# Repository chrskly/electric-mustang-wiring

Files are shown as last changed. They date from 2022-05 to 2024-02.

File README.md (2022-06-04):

# Electric Mustang Wiring

This repo contains the circuits, software, and wiring diagrams for my project to
convert a 1965 Ford Mustang to a EV.

## bms - Battery Management System

Schematic, PCB, and software for the battery management system.

## 12v-front-pcb

Schematic and PCB for wiring that sits in the front of the car (engine bay).

* Ignition switch
* Drive inhibition (preventing driving off when charging)
* Coolant pump
* Inverter
* Contactors
* Shunt

## 12v-lighting

Schematic and PCB for wiring for all of the lighting.

* Headlights/highbeams
* Indicators
* Brake lights
* Interior lights

## 12v-rear-pcb

Schematic and PCB for wiring that sits in the rear of the car (boot).

* On-board AC charger
* DC charger
* Charger VCU

## dashboard-vcu

Schematic and PCB for VCU to control the car dashboard.

## dashboard-vcu-src

Source code of dashboard vcu firmware.

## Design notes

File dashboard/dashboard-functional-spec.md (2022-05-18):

# Functional spec for dashboard

I want the interior of the car to remain original, or, at least, feel original.
No screens. The existing gauges and dash lights are more than enough to use the
car for normal driving. The dashboard will provide an additional web interface
for when I need to inspect the details of the cars operation.

Dashboard will need to stay on all of the time, but can possibly switch to a
lower power mode when car is not driving/charging.

## Physical dash functionality

1. Read SoC from ISA shunt and show on fuel gauge.

2. Show max of all temps on temp gauge (what temps will be available?)

3. Show car mode on left dash indicator.
  - Orange : ignition on, but inverter not in run mode
  - Green  : ignition on, inverter in run mode
  - Blue   : charging

4. Show car status on right dash indicator.
  - Green  : car healthy
  - Orange : warning message from one of the car systems
  - Red    : critical error from one of the car systems

Note : I could possibly show all of this with one dash light. If so, what would
I use the other one for?

5. Stepper motor to drive speedo/odometer.

6. Data logger.

7. GPS?

## Web dash functionality

1. Provide WiFi hotspot. esp8266 or similar.

2. Show pack voltage.

3. Show pack SoC.

4. Show current power in/out.

5. Charging : status

6. Charging : eta to 80%, 100%

7. Driving : estimated range, time to empty.

8. Logs

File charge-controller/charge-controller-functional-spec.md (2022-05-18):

# Functional spec for charge controller

Charge controller will manage LIM unit for DC charging and Tesla v2 unit for
AC charging.

## Functionality

1. Measure temp of charge port.

2. Limit charging rate based on battery temp.

## Connections

1. CAN port connected to main CAN bus.

2. CAN port connected to Tesla gen 2 OBC.

3. CAN port connected to LIM.

4. 2x thermistor inputs.

5. Stop charge input.

## CAN messages consumed by charge controller

1. BMS temperature readings.

## CAN messages produced by charge controller

1. Control messages for LIM

2. Control messages for Tesla charger

## External resources

### Damien's LIM control implementation for Zombieverter

https://github.com/damienmaguire/Stm32-vcu/blob/master/src/i3LIM.cpp

### OpenInverter forum LIM docs

https://openinverter.org/wiki/BMW_I3_Fast_Charging_LIM_Module

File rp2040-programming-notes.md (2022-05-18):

## Pinout

http://land-boards.com/blwiki/images/thumb/5/56/Raspberry-Pi-Pico-Pinout.jpg/730px-Raspberry-Pi-Pico-Pinout.jpg

## Repeating timers

https://emalliab.wordpress.com/2021/04/18/raspberry-pi-pico-arduino-core-and-timers/

https://raspberrypi.github.io/pico-sdk-doxygen/group__repeating__timer.html#ga02133dbe7083fcf3c7392a2cfb8243ba

## Changing PWM frequency

https://www.pschatzmann.ch/home/2021/05/19/back-to-basics-audio-output-on-the-raspberry-pico/

## mcp2515

https://github.com/autowp/arduino-mcp2515

https://github.com/adamczykpiotr/pico-mcp2515

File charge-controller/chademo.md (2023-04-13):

# Chademo

## Chademo pinout

 1. Ground
 2. CP : evse => car, IN1, contactor +ve signal, goes high when active, sensed by 'f'
 3. nc
 4. CP3 : car => evse, OUT1, charge enable, sensed by 'k'
 5. HV-
 6. HV+
 7. CS : connection check, goes low when plug inserted, sensed by 'h'
 8. CAN H
 9. CAN L
10. CP2 : evse => car, IN2, contactor -ve signal, goes low when active, sensed by 'g'

OUT2, contactor override, pull low to allow CP2 signal through

## Charging sequence

- station pulls CS high?low? to indicate plug insertion
- station pulls CP high (IN1), d1 closes, +ve contactor closes
- Start CAN
- Station/car send params, compatability check
- car pulls CP3 low to indicate start permission
- connector lock
- station runs insulation test
- station pulls CP2 low (IN2), d2 closes
- << charging >>
- car sends current request constantly
- battery fills up, car sends zero current request
- car deactivates CP3, stop permission
- station deactivates CP and CP2
- weld detection?
- unlock

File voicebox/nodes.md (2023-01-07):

https://gregchadwick.co.uk/blog/playing-with-the-pico-pt3/

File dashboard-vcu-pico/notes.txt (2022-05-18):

https://raspberrypi.github.io/pico-sdk-doxygen/modules.html
https://raspberrypi.github.io/pico-sdk-doxygen/rp2__common_2hardware__spi_2include_2hardware_2spi_8h.html
http://docs.longan-labs.cc/1030018/
https://www.hackster.io/fhdm-dev/use-arduino-libraries-with-the-rasperry-pi-pico-c-c-sdk-eff55c
https://fhdm-dev.github.io/pico-arduino-compat/libraries.html
https://github.com/fhdm-dev/pico-arduino-compat/tree/master/libs/adafruit-ssd1306
https://github.com/107-systems/107-Arduino-MCP2515

https://copperhilltech.com/pican-2-can-bus-interface-for-raspberry-pi/
https://copperhilltech.com/blog/obdii-data-logging-with-raspberry-pi-and-pican2-can-bus-interface/
https://copperhilltech.com/blog/troubleshooting-your-pican2-can-interface-board-for-raspberry-pi/

### Pico PIO
https://www.digikey.com/en/maker/projects/raspberry-pi-pico-and-rp2040-cc-part-3-how-to-use-pio/123ff7700bc547c79a504858c1bd8110

### Pico SDK
https://raspberrypi.github.io/pico-sdk-doxygen/group__hardware__gpio.html#ga594e390dc5e7407a35bcce6cae73ae2c

### Catphish bms
https://github.com/catphish/ev-charge-controller/blob/master/firmware-pico/bms.c

### Getting started with Pico
https://datasheets.raspberrypi.com/pico/getting-started-with-pico.pdf

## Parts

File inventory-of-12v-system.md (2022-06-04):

# Inventory of 12v system

## Engine bay (front-12v)
- [x] Ignition
- [x] Inverter
- [x] ISA shunt (always on)
- [x] Contactors
- [x] Coolant pump
- [x] Drive inhibit

## Cabin
- [ ] Brake
- [ ] Radio
- [ ] Cabin water heater
- [ ] Cabin fan
- [ ] Dashboard (always on)
- [ ] Horn
- [ ] Wipers
- [ ] Cruise

## Lights
- [x] Headlights/highbeams (10A)
- [x] Indicators
- [x] Flashers
- [ ] Brake lights
- [ ] Reverse light
- [x] Cabin light (+glovebox)
- [ ] Engine bay light

## Rear
- [ ] Trunk light
- [ ] Tesla
- [ ] LIM
- [ ] BMS (always on)

## Others
- [ ] Vacuum pump
- [ ] Heated seats

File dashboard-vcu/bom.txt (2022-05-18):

Component, Value, Part #, Footprint
U1, rPi Pico
D2, n/a, SS54B, DIOM5336X244N
PS1, n/a, TPS62160DGKT, TPS62160DGKT
C1, 10uF, CL10A106KP8NNNC, 
C2, 22uF, 
L1, 2.2uH, NR6028T2R2N, 
R1, 1k
R2, R3, 2k2,
R4 + R5 + R6 + R7 + R8 + R9, 220, 
R10, 100k, 
R11, 220k,
R12, 47k, 

J1, Molex 39300140

https://datasheet.lcsc.com/lcsc/2004061032_MOLEX-39300140_C492360.pdf
https://jlcpcb.com/parts/componentSearch?isSearch=true&searchTxt=XAL6030-222MEB
https://www.electronicshub.org/arduino-mcp2515-can-bus-tutorial/
https://www.sparkfun.com/datasheets/DevTools/Arduino/MCP2515.pdf
https://imgur.com/a/pi17C7X

https://www.digikey.be/en/maker/projects/raspberry-pi-pico-rp2040-spi-example-with-micropython-and-cc/9706ea0cf3784ee98e35ff49188ee045

https://raspberrypi.github.io/pico-sdk-doxygen/modules.html

Ampseal35, 1.3mm tin 8A, 1.3mm gold 17A

8 circuit molex, high current connections
https://ie.rs-online.com/web/p/pcb-headers/1615968
https://ie.rs-online.com/web/p/pcb-headers/1615961
https://www.molex.com/molex/products/part-detail/pcb_headers/1720650208
https://www.molex.com/molex/products/part-detail/crimp_housings/1700010108
https://www.molex.com/molex/products/part-detail/crimp_terminals/1720630311
https://componentsearchengine.com/part-view/172065-0208/Molex

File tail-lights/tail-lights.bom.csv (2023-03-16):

Comment | Designator | Footprint | LCSC
HL-AM-2835H421W-S1-08-HR3 | LED1,LED2,LED3,LED4,LED5,LED6,LED7,LED8,LED9,LED10,LED11,LED12,LED13,LED14,LED15,LED16,LED17,LED18,LED19,LED20,LED21,LED22,LED23,LED24,LED25,LED26,LED27,LED28,LED29,LED30,LED31,LED32,LED33,LED34,LED35,LED36,LED37,LED38,LED39,LED40,LED41,LED42,LED43,LED44,LED45,LED46,LED47,LED48,LED49,LED50,LED51,LED52,LED53,LED54,LED55,LED56,LED57,LED58,LED59,LED60,LED61,LED62,LED63,LED64,LED65,LED66,LED67,LED68,LED69,LED70,LED71,LED72 | SMD2835 | C210318
NCV8402ASTT1G | IC2,IC3,IC4 | SOT223 | C77755
ATMEGA328P-AU | IC1 | TQFP-32 | C14877
4k7Ω | R1,R2,R3 | 0805_R | C17673
1k5Ω | R4,R5,R6 | 0805_R | C4310
1uF | C1,C2,C3 | 0805_C | C28323
X322516MLB4SI | Y1 | SMD3225-4P | C13738
10kΩ | R7,R8,R9 | 0805_R | C84376
0.1uF | C4,C5 | 0805_C | C49678
TPS62160DGKR | IC5 | MSOP-8 | C60726
10uF | C6 | 0805_C | C15850
100kΩ | R10 | 0805_R | C149504
2.2uH | L1 | SMD | C135262
220kΩ | R11 | 0805_R | C17539
47kΩ | R12 | 0805_R | C17713
22uF | C7 | 0805_C | C2835558

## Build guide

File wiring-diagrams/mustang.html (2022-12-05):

# mustang

## Diagram

## Bill of Materials

Id | Description | Qty | Unit | Designators
1 | Cable, 1 x 1 mm² | 0 | m | IGNITION_START, W14
2 | Cable, 1 x 6 mm² | 0 | m | W5, W6
3 | Cable, 2 x 1 mm² | 0 | m | IGNITION, W12, W13, W15, W22, W26, W28, W8
4 | Cable, 2 x 10 mm² | 0 | m | W27
5 | Cable, 2 x 35 mm² | 0 | m | W10, W23, W24, W25
6 | Cable, 2 x 6 mm² | 0 | m | W3
7 | Cable, 2 x 70 mm² | 0 | m | W29, W30
8 | Cable, 3 x 1 mm² | 0 | m | W7
9 | Cable, 3 x 2.5 mm² | 0 | m | W16, W17, W18, W19, W20, W21
10 | Cable, 4 x 0.25 mm² | 0 | m | W4
11 | Cable, 4 x 1 mm² | 0 | m | W11, W9
12 | Cable, 8 x 0.25 mm² shielded | 0 | m | W1, W2
13 | Connector, 10 pins | 1 | | TESLA_CHARGER_A
14 | Connector, 12 pins | 1 | | TESLA_CHARGER_B
15 | Connector, 2 pins | 7 | | CHADEMO_CHARGE_PORT, CHARGER_FUSE_1, CHARGER_FUSE_2, CHARGER_FUSE_3, CHARGER_MCB_1, CHARGER_MCB_2, CHARGER_MCB_3
16 | Connector, 2pin, 2 pins | 1 | | 12VBATT
17 | Connector, 3 pins | 1 | | LIM_VOLTAGE_SENSE_2
18 | Connector, 4 pins | 1 | | LIM_VOLTAGE_SENSE_1
19 | Connector, 6 pins | 4 | | FRONT_BATTERY_BOX, REAR_BATTERY_BOX, TESLA_CHARGER_AC, TESLA_CHARGER_DC
20 | Connector, 8 pins | 1 | | CCS_HVJB
21 | Connector, 8pin, 31 pins | 1 | | HVJB
22 | Connector, 8pin, male, 8 pins | 2 | | MG1RES, MG2RES
23 | Connector, 9 pins | 1 | | CCS_CHARGE_PORT
24 | Connector, Ampseal-35, male, 35 pins | 1 | | AMPSEAL_35_1
25 | Connector, Hirschmann 805-587-545, 16 pins | 1 | | LIM_1B
26 | Connector, Molex MegaFit, 2 pins | 8 | | 12V_REAR_J2, 12V_REAR_J3, 12V_REAR_J4, 12V_REAR_J5, 12V_REAR_J6, 12V_REAR_J7, 12V_REAR_J8, 12V_REAR_J9
27 | Connector, Molex MegaFit, 4 pins | 1 | | 12V_REAR_J10
28 | Connector, Molex MegaFit, male, 2 pins | 3 | | 12V_FRONT_J1, 12V_FRONT_J5, 12V_FRONT_J7
29 | Connector, Molex MegaFit, male, 4 pins | 4 | | 12V_FRONT_J2, 12V_FRONT_J3, 12V_FRONT_J4, 12V_FRONT_J6
30 | Connector, SUMITOMO 90980-12362, 8 pins | 1 | | SHIFTER
31 | Connector, Switch, 3 pins | 1 | | IGNITION_SW
32 | Connector, TE 1-967616-1, 6 pins | 1 | | LIM_2B
33 | Connector, TE 1534152-1, 12 pins | 1 | | LIM_4B

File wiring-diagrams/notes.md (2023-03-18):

Colors
WH white
BN brown
GN green
BK black
RD red
YE yellow
BU blue
OG orange
VT violet
GD gold
GY grey

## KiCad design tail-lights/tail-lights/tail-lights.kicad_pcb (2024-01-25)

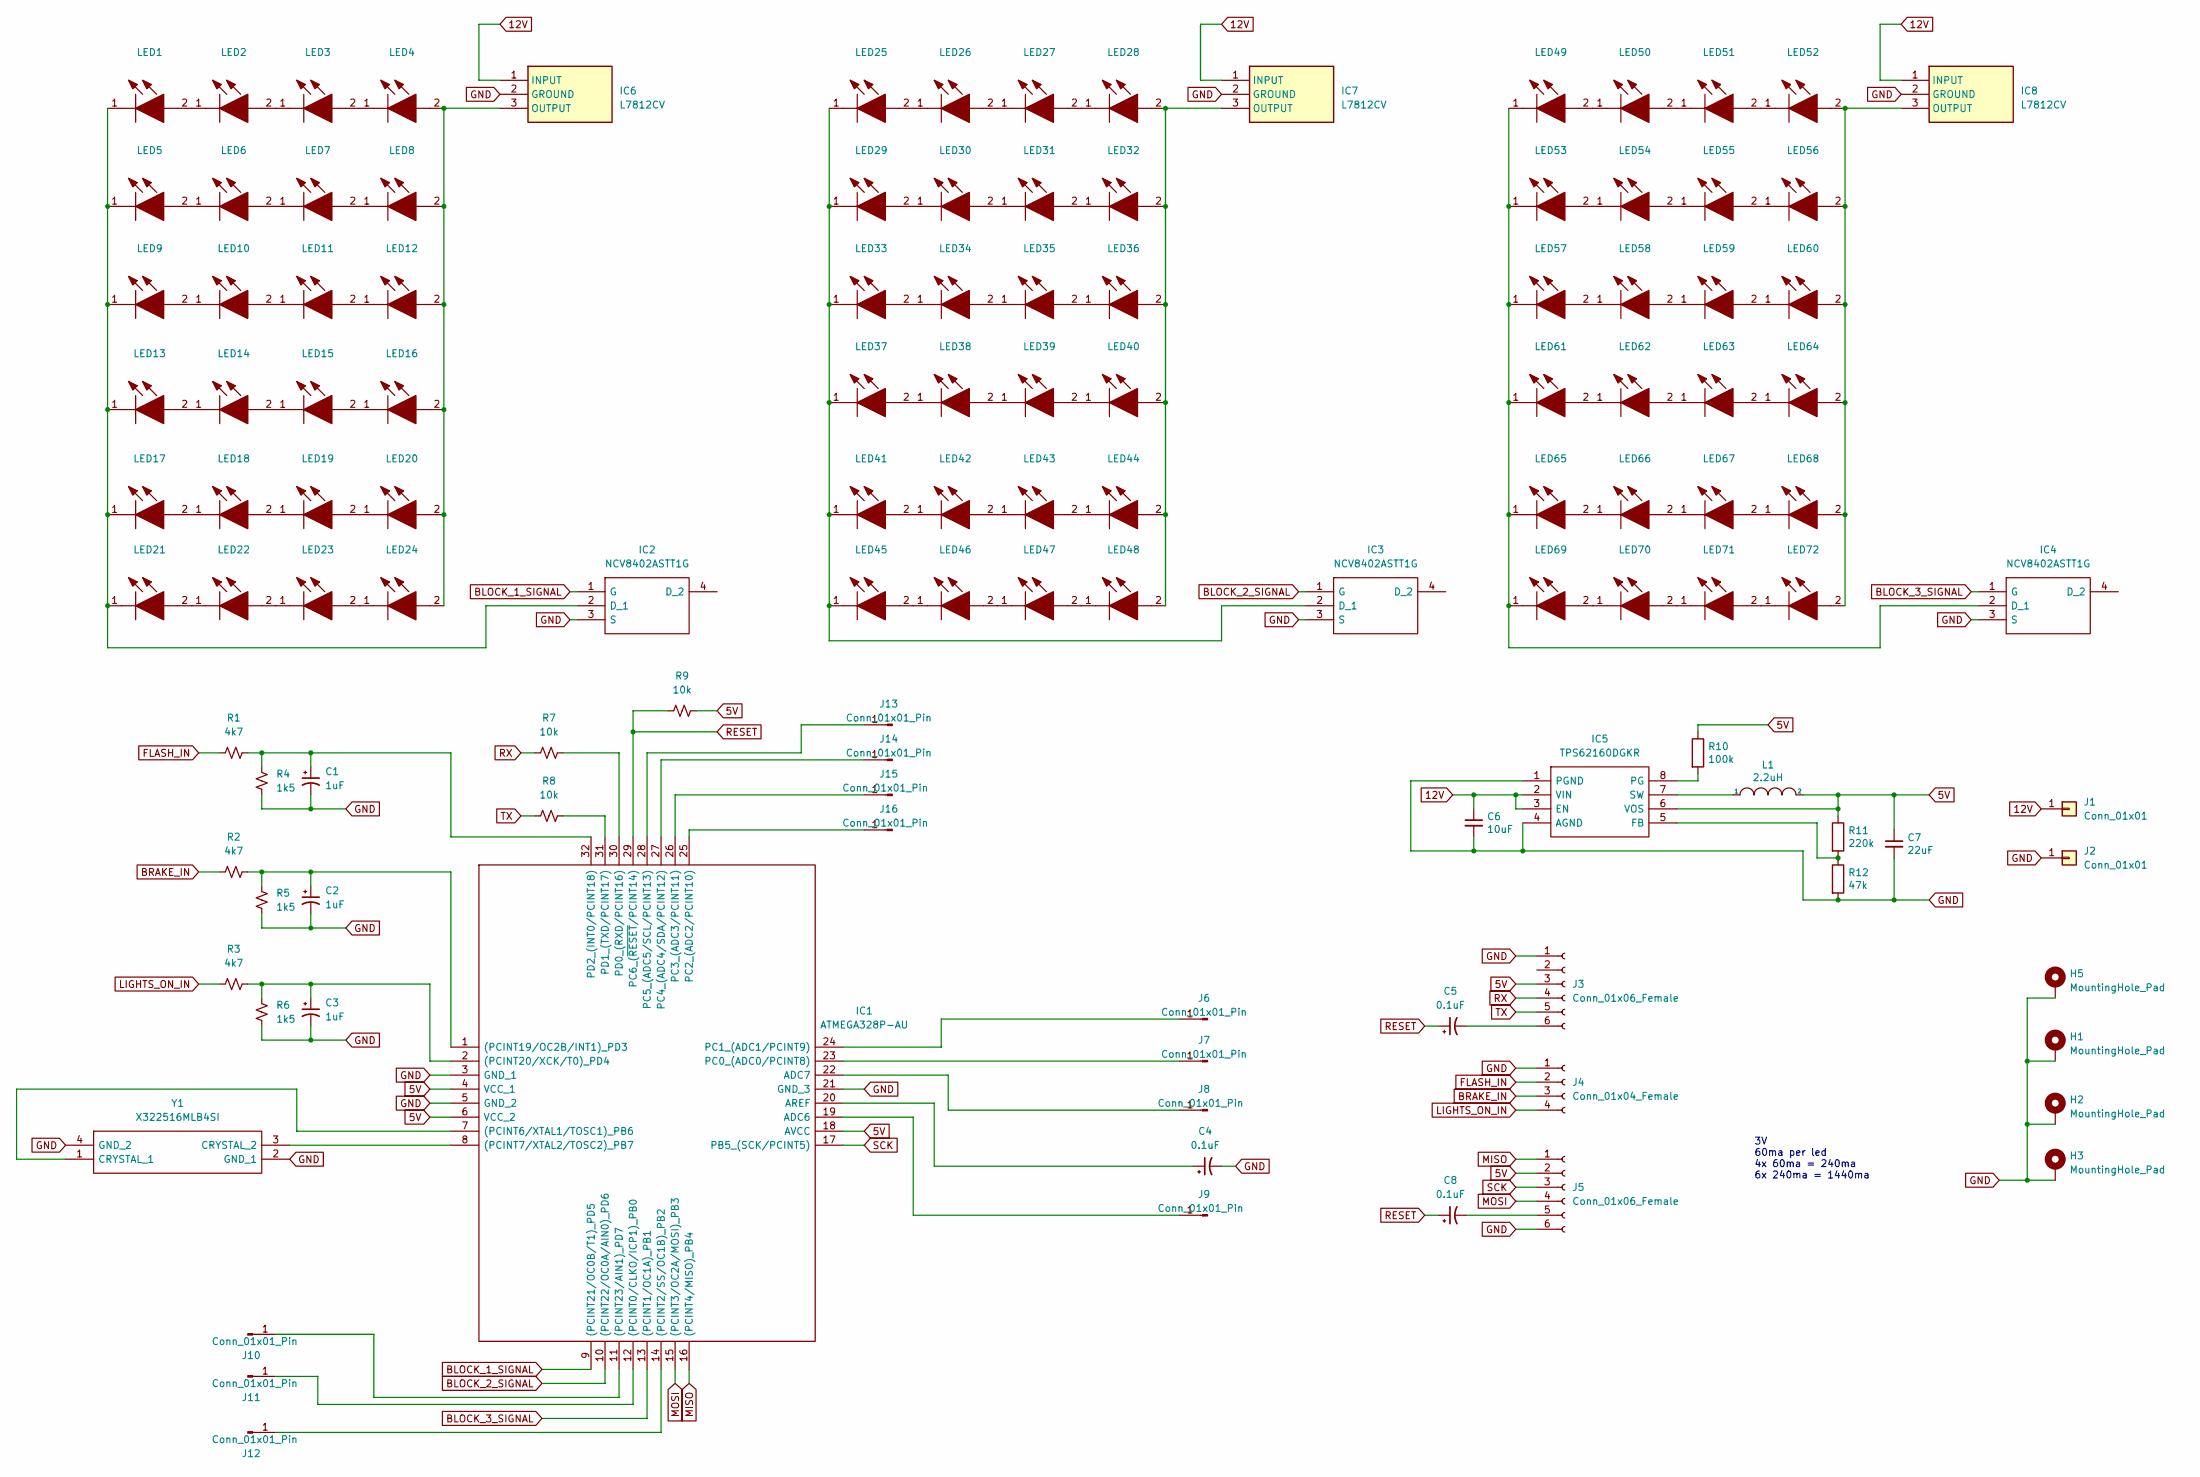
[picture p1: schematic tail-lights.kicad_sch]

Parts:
C1, C2, C3: 1uF; C_0603_1608Metric
C4, C5, C8: 0.1uF; C_0603_1608Metric
C6: 10uF; C_0603_1608Metric
C7: 22uF; C_0805_2012Metric
H1, H2, H3, H5: MountingHole_Pad; MountingHole_2.5mm_Pad
IC1: ATMEGA328P-AU; QFP80P900X900X120-32N; Manufacturer_Part_Number ATMEGA328P-AU; Mouser Part Number 556-ATMEGA328P-AU
IC2, IC3, IC4: NCV8402ASTT1G; SOT230P700X175-4N; Manufacturer_Part_Number NCV8402ASTT1G; Mouser Part Number 863-NCV8402ASTT1G
IC5: TPS62160DGKR; SOP65P490X110-8N; Manufacturer_Part_Number TPS62160DGKR; Mouser Part Number 595-TPS62160DGKR
IC6, IC7, IC8: L7812CV; TO255P460X1020X2008-3P; Manufacturer_Part_Number L7812CV; Mouser Part Number 511-L7812CV
J1, J2: Conn_01x01; SolderWire-1sqmm_1x01_D1.4mm_OD2.7mm
J3, J5: Conn_01x06_Female; PinHeader_1x06_P2.54mm_Vertical
J4: Conn_01x04_Female; PinHeader_1x04_P2.54mm_Vertical
J6, J7, J8, J9, J10, J11, J12, J13, J14, J15, J16: Conn_01x01_Pin; PinHeader_1x01_P2.54mm_Vertical
L1: 2.2uH; NR6028T220M
LED1, LED2, LED3, LED4, LED5, LED6, LED7, LED8, LED9, LED10, LED11, LED12, LED13, LED14, LED15, LED16, LED17, LED18, LED19, LED20, LED21, LED22, LED23, LED24, LED25, LED26, LED27, LED28, LED29, LED30, LED31, LED32, LED33, LED34, LED35, LED36, LED37, LED38, LED39, LED40, LED41, LED42, LED43, LED44, LED45, LED46, LED47, LED48, LED49, LED50, LED51, LED52, LED53, LED54, LED55, LED56, LED57, LED58, LED59, LED60, LED61, LED62, LED63, LED64, LED65, LED66, LED67, LED68, LED69, LED70, LED71, LED72: HL-AM-2835H421W-S1-08-HR3; HLAM2835H421WS108HR3; Manufacturer_Part_Number HL-AM-2835H421W-S1-08-HR3
R1, R2, R3: 4k7; R_0805_2012Metric
R4, R5, R6: 1k5; R_0805_2012Metric
R7, R8, R9: 10k; R_0805_2012Metric
R10: 100k; R_0805_2012Metric
R11: 220k; R_0805_2012Metric
R12: 47k; R_0805_2012Metric
Y1: X322516MLB4SI; Manufacturer_Part_Number X322516MLB4SI

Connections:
5V: C7.1, IC1.4 (VCC_1), IC1.6 (VCC_2), IC1.18 (AVCC), IC5.6 (VOS), J3.3, J5.2, L1.2, R9.2, R10.1, R11.1
12V: C6.1, IC5.2 (VIN), IC5.3 (EN), IC6.1 (INPUT), IC7.1 (INPUT), IC8.1 (INPUT), J1.1
BLOCK_1_SIGNAL: IC1.9 ((PCINT21/OC0B/T1)_PD5), IC2.1 (G)
BLOCK_2_SIGNAL: IC1.10 ((PCINT22/OC0A/AIN0)_PD6), IC3.1 (G)
BLOCK_3_SIGNAL: IC1.13 ((PCINT1/OC1A)_PB1), IC4.1 (G)
BRAKE_IN: J4.3, R2.1
FLASH_IN: J4.2, R1.1
GND: C1.2, C2.2, C3.2, C4.2, C6.2, C7.2, H1.1, H2.1, H3.1, H5.1, IC1.3 (GND_1), IC1.5 (GND_2), IC1.21 (GND_3), IC2.3 (S), IC3.3 (S), IC4.3 (S), IC5.1 (PGND), IC5.4 (AGND), IC6.2 (GROUND), IC7.2 (GROUND), IC8.2 (GROUND), J2.1, J3.1, J4.1, J5.6, R4.2, R5.2, R6.2, R12.2, Y1.2 (GND_1), Y1.4 (GND_2)
LIGHTS_ON_IN: J4.4, R3.1
MISO: IC1.16 ((PCINT4/MISO)_PB4), J5.1
MOSI: IC1.15 ((PCINT3/OC2A/MOSI)_PB3), J5.4
unnamed: IC1.12 ((PCINT0/CLKO/ICP1)_PB0), J11.1
unnamed: IC1.14 ((PCINT2/SS/OC1B)_PB2), J12.1
unnamed: IC1.7 ((PCINT6/XTAL1/TOSC1)_PB6), Y1.1 (CRYSTAL_1)
unnamed: IC1.8 ((PCINT7/XTAL2/TOSC2)_PB7), Y1.3 (CRYSTAL_2)
unnamed: C2.1, IC1.1 ((PCINT19/OC2B/INT1)_PD3), R2.2, R5.1
unnamed: C3.1, IC1.2 ((PCINT20/XCK/T0)_PD4), R3.2, R6.1
unnamed: IC1.11 ((PCINT23/AIN1)_PD7), J10.1
unnamed: IC1.19 (ADC6), J9.1
unnamed: IC1.22 (ADC7), J8.1
unnamed: C4.1, IC1.20 (AREF)
unnamed: IC1.23 (PC0_(ADC0/PCINT8)), J7.1
unnamed: IC1.24 (PC1_(ADC1/PCINT9)), J6.1
unnamed: IC1.25 (PC2_(ADC2/PCINT10)), J16.1
unnamed: IC1.26 (PC3_(ADC3/PCINT11)), J15.1
unnamed: IC1.27 (PC4_(ADC4/SDA/PCINT12)), J14.1
unnamed: IC1.28 (PC5_(ADC5/SCL/PCINT13)), J13.1
unnamed: IC1.30 (PD0_(RXD/PCINT16)), R7.2
unnamed: IC1.31 (PD1_(TXD/PCINT17)), R8.2
unnamed: C1.1, IC1.32 (PD2_(INT0/PCINT18)), R1.2, R4.1
unnamed: IC2.2 (D_1), LED1.1, LED5.1, LED9.1, LED13.1, LED17.1, LED21.1
unnamed: IC3.2 (D_1), LED25.1, LED29.1, LED33.1, LED37.1, LED41.1, LED45.1
unnamed: IC4.2 (D_1), LED49.1, LED53.1, LED57.1, LED61.1, LED65.1, LED69.1
unnamed: IC5.5 (FB), R11.2, R12.1
unnamed: IC5.8 (PG), R10.2
unnamed: IC5.7 (SW), L1.1
unnamed: IC6.3 (OUTPUT), LED4.2, LED8.2, LED12.2, LED16.2, LED20.2, LED24.2
unnamed: IC7.3 (OUTPUT), LED28.2, LED32.2, LED36.2, LED40.2, LED44.2, LED48.2
unnamed: IC8.3 (OUTPUT), LED52.2, LED56.2, LED60.2, LED64.2, LED68.2, LED72.2
unnamed: C5.2, J3.6
unnamed: C8.2, J5.5
unnamed: LED1.2, LED2.1
unnamed: LED2.2, LED3.1
unnamed: LED3.2, LED4.1
unnamed: LED5.2, LED6.1
unnamed: LED6.2, LED7.1
unnamed: LED7.2, LED8.1
unnamed: LED9.2, LED10.1
unnamed: LED10.2, LED11.1
unnamed: LED11.2, LED12.1
unnamed: LED13.2, LED14.1
unnamed: LED14.2, LED15.1
unnamed: LED15.2, LED16.1
unnamed: LED17.2, LED18.1
unnamed: LED18.2, LED19.1
unnamed: LED19.2, LED20.1
unnamed: LED21.2, LED22.1
unnamed: LED22.2, LED23.1
unnamed: LED23.2, LED24.1
unnamed: LED25.2, LED26.1
unnamed: LED26.2, LED27.1
unnamed: LED27.2, LED28.1
unnamed: LED29.2, LED30.1
unnamed: LED30.2, LED31.1
unnamed: LED31.2, LED32.1
unnamed: LED33.2, LED34.1
unnamed: LED34.2, LED35.1
unnamed: LED35.2, LED36.1
unnamed: LED37.2, LED38.1
unnamed: LED38.2, LED39.1
unnamed: LED39.2, LED40.1
unnamed: LED41.2, LED42.1
unnamed: LED42.2, LED43.1
unnamed: LED43.2, LED44.1
unnamed: LED45.2, LED46.1
unnamed: LED46.2, LED47.1
unnamed: LED47.2, LED48.1
unnamed: LED49.2, LED50.1
unnamed: LED50.2, LED51.1
unnamed: LED51.2, LED52.1
unnamed: LED53.2, LED54.1
unnamed: LED54.2, LED55.1
unnamed: LED55.2, LED56.1
unnamed: LED57.2, LED58.1
unnamed: LED58.2, LED59.1
unnamed: LED59.2, LED60.1
unnamed: LED61.2, LED62.1
unnamed: LED62.2, LED63.1
unnamed: LED63.2, LED64.1
unnamed: LED65.2, LED66.1
unnamed: LED66.2, LED67.1
unnamed: LED67.2, LED68.1
unnamed: LED69.2, LED70.1
unnamed: LED70.2, LED71.1
unnamed: LED71.2, LED72.1
RESET: C5.1, C8.1, IC1.29 (PC6_(~RESET/PCINT14)), R9.1
RX: J3.4, R7.1
SCK: IC1.17 (PB5_(SCK/PCINT5)), J5.3
TX: J3.5, R8.1

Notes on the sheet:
3V 60ma per led 4x 60ma = 240ma 6x 240ma = 1440ma

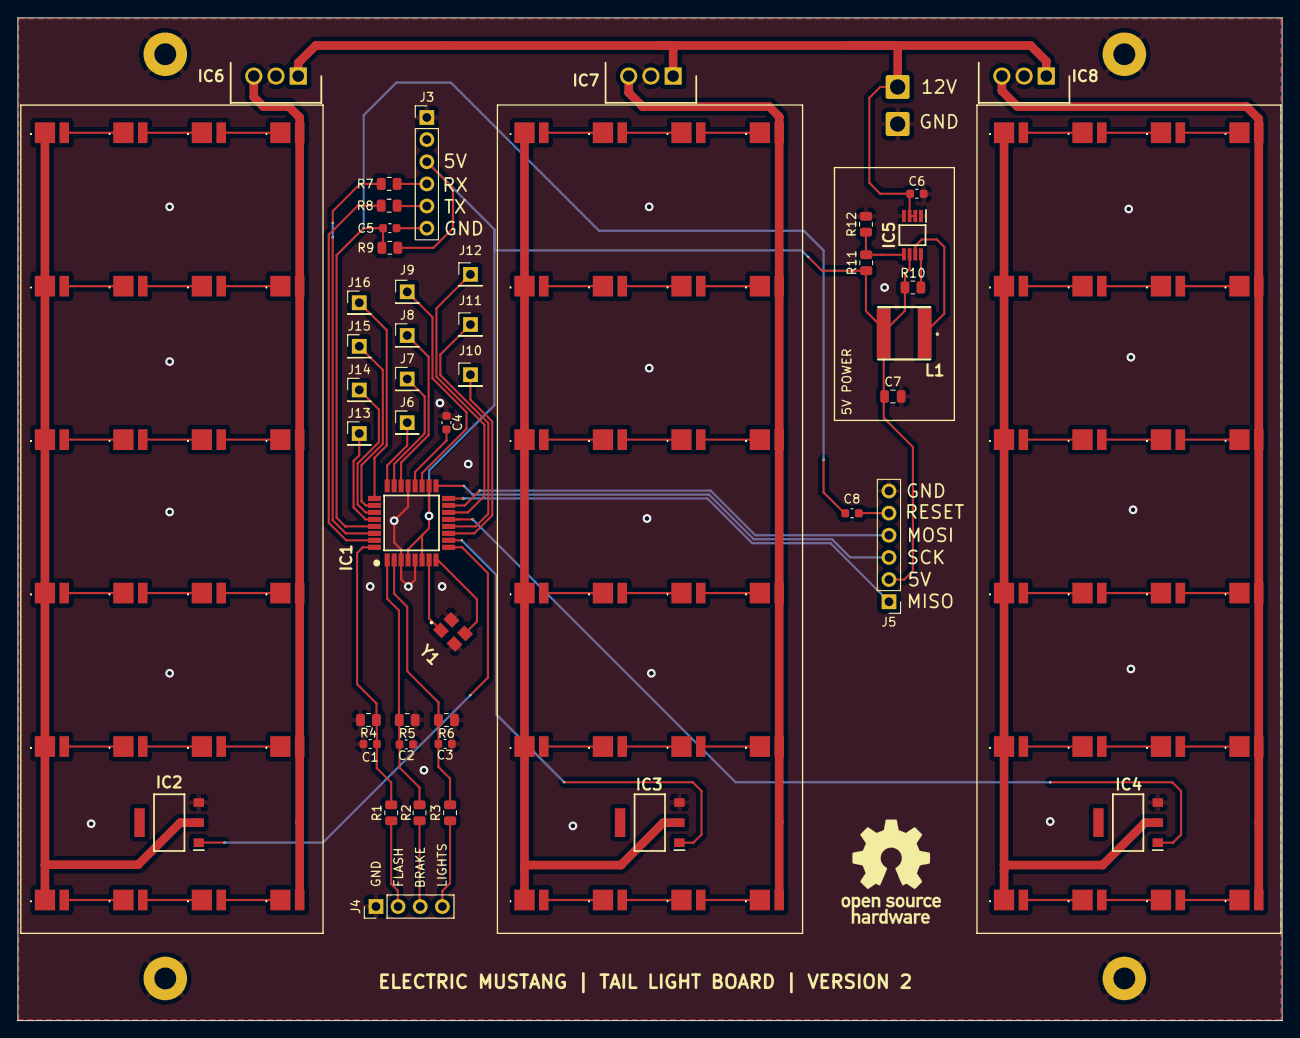
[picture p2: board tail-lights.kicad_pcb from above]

Board: 2 copper layers, 145.0 x 115.0 mm, 122 parts (0 on the bottom side), 99 nets.

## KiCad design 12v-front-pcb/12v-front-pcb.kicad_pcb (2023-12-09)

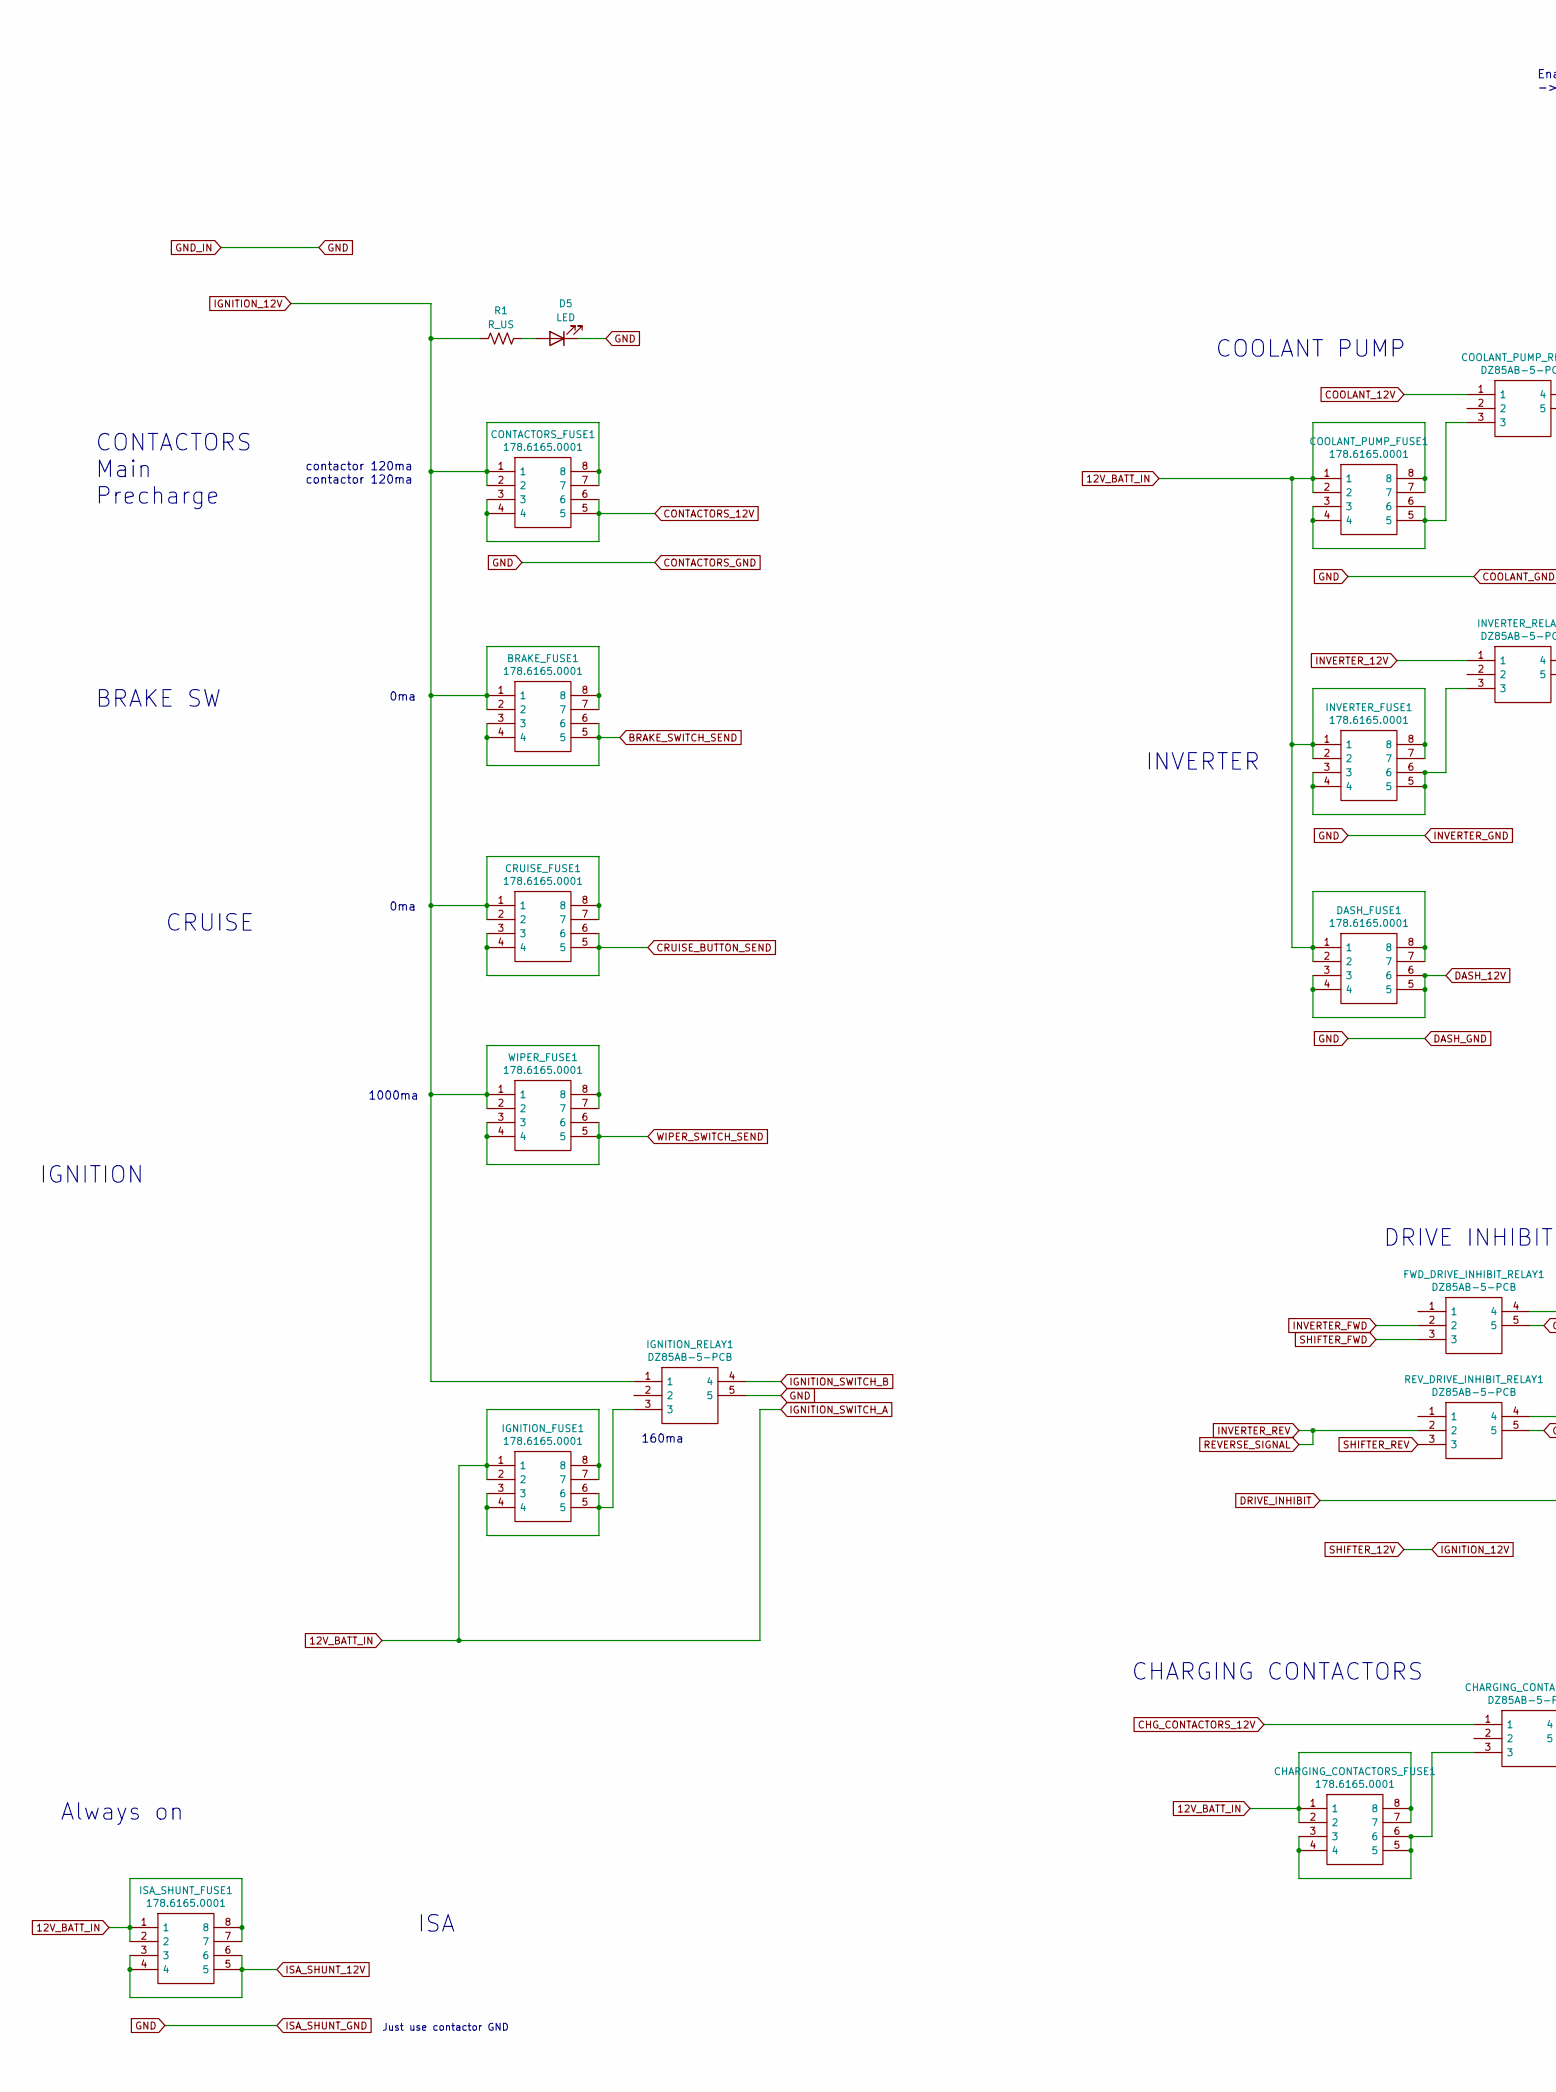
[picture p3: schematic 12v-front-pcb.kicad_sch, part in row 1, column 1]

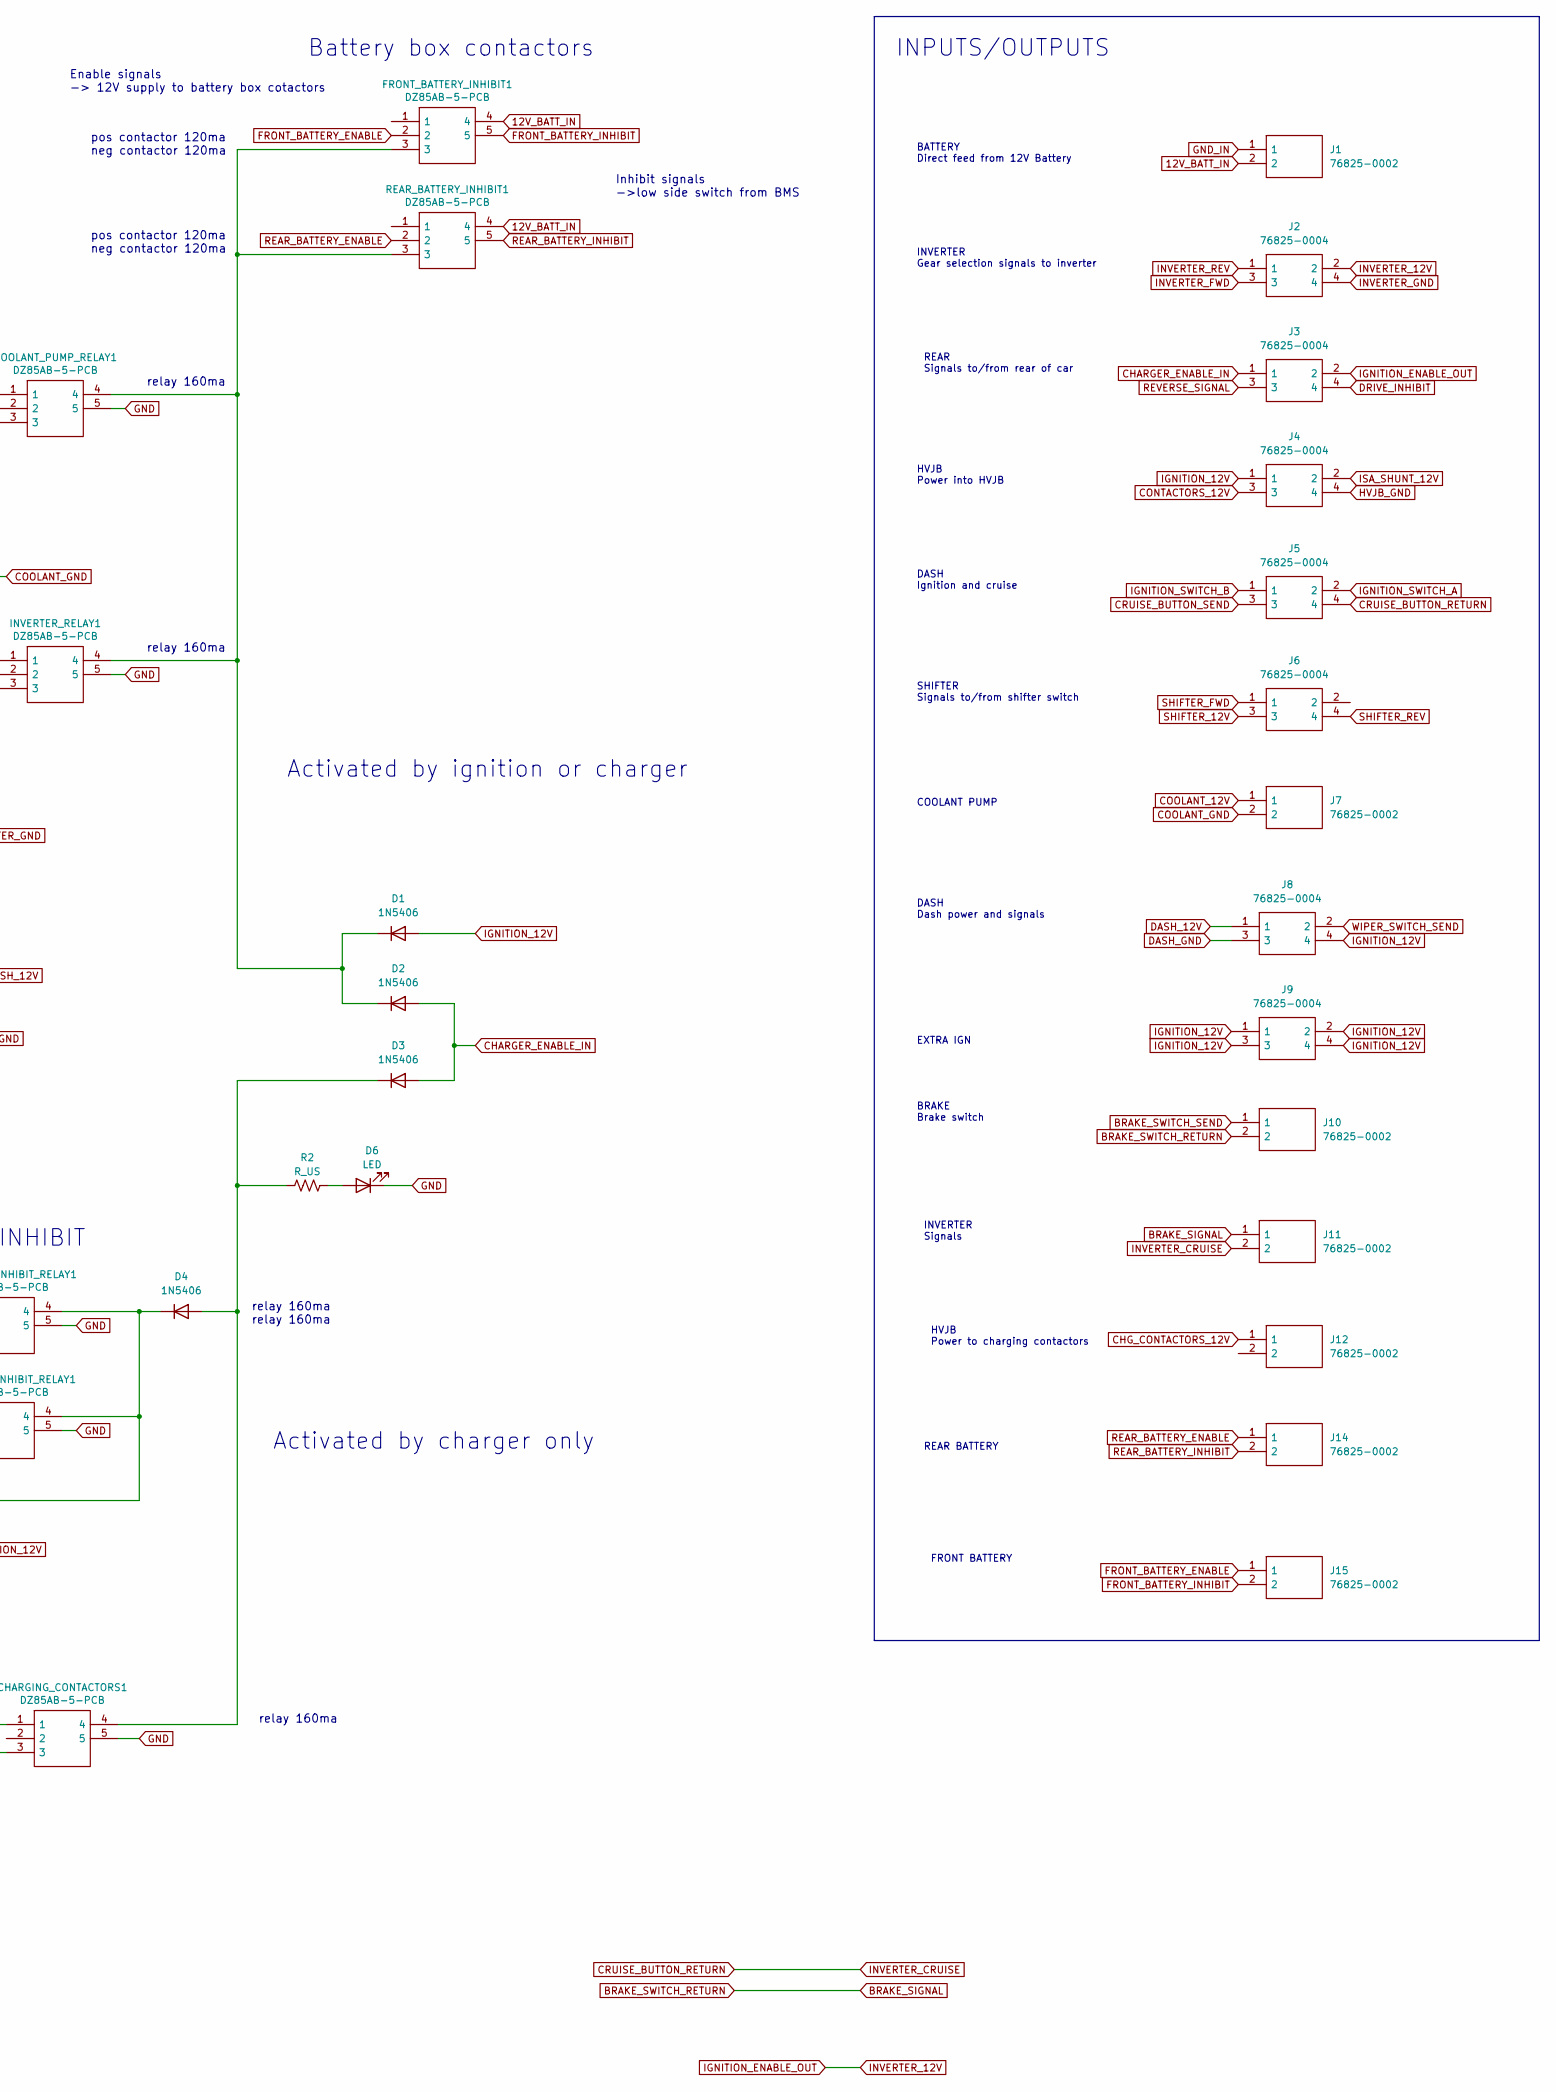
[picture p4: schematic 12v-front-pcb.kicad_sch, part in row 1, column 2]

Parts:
BRAKE_FUSE1: 178.6165.0001; 17861650001; Manufacturer_Part_Number 178.6165.0001; Mouser Part Number 576-178.6165.0001
CHARGING_CONTACTORS1: DZ85AB-5-PCB; DZ85AB5PCB; Manufacturer_Part_Number DZ85AB-5-PCB
CHARGING_CONTACTORS_FUSE1: 178.6165.0001; 17861650001; Manufacturer_Part_Number 178.6165.0001; Mouser Part Number 576-178.6165.0001
CONTACTORS_FUSE1: 178.6165.0001; 17861650001; Manufacturer_Part_Number 178.6165.0001; Mouser Part Number 576-178.6165.0001
COOLANT_PUMP_FUSE1: 178.6165.0001; 17861650001; Manufacturer_Part_Number 178.6165.0001; Mouser Part Number 576-178.6165.0001
COOLANT_PUMP_RELAY1: DZ85AB-5-PCB; DZ85AB5PCB; Manufacturer_Part_Number DZ85AB-5-PCB
CRUISE_FUSE1: 178.6165.0001; 17861650001; Manufacturer_Part_Number 178.6165.0001; Mouser Part Number 576-178.6165.0001
D1, D2, D3, D4: 1N5406; D_DO-201AD_P15.24mm_Horizontal
D5, D6: LED; LED_D3.0mm_Clear
DASH_FUSE1: 178.6165.0001; 17861650001; Manufacturer_Part_Number 178.6165.0001; Mouser Part Number 576-178.6165.0001
FRONT_BATTERY_INHIBIT1: DZ85AB-5-PCB; DZ85AB5PCB; Manufacturer_Part_Number DZ85AB-5-PCB
FWD_DRIVE_INHIBIT_RELAY1: DZ85AB-5-PCB; DZ85AB5PCB; Manufacturer_Part_Number DZ85AB-5-PCB
IGNITION_FUSE1: 178.6165.0001; 17861650001; Manufacturer_Part_Number 178.6165.0001; Mouser Part Number 576-178.6165.0001
IGNITION_RELAY1: DZ85AB-5-PCB; DZ85AB5PCB; Manufacturer_Part_Number DZ85AB-5-PCB
INVERTER_FUSE1: 178.6165.0001; 17861650001; Manufacturer_Part_Number 178.6165.0001; Mouser Part Number 576-178.6165.0001
INVERTER_RELAY1: DZ85AB-5-PCB; DZ85AB5PCB; Manufacturer_Part_Number DZ85AB-5-PCB
ISA_SHUNT_FUSE1: 178.6165.0001; 17861650001; Manufacturer_Part_Number 178.6165.0001; Mouser Part Number 576-178.6165.0001
J1, J7, J10, J11, J12, J14, J15: 76825-0002; 768250002; Manufacturer_Part_Number 76825-0002; Mouser Part Number 538-76825-0002
J2, J3, J4, J5, J6, J8, J9: 76825-0004; 768250004; Manufacturer_Part_Number 76825-0004; Mouser Part Number 538-76825-0004
R1, R2: R_US; D_T-1_P2.54mm_Vertical_AnodeUp
REAR_BATTERY_INHIBIT1: DZ85AB-5-PCB; DZ85AB5PCB; Manufacturer_Part_Number DZ85AB-5-PCB
REV_DRIVE_INHIBIT_RELAY1: DZ85AB-5-PCB; DZ85AB5PCB; Manufacturer_Part_Number DZ85AB-5-PCB
WIPER_FUSE1: 178.6165.0001; 17861650001; Manufacturer_Part_Number 178.6165.0001; Mouser Part Number 576-178.6165.0001

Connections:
12V_BATT_IN: CHARGING_CONTACTORS_FUSE1.1, CHARGING_CONTACTORS_FUSE1.2, CHARGING_CONTACTORS_FUSE1.7, CHARGING_CONTACTORS_FUSE1.8, COOLANT_PUMP_FUSE1.1, COOLANT_PUMP_FUSE1.2, COOLANT_PUMP_FUSE1.7, COOLANT_PUMP_FUSE1.8, DASH_FUSE1.1, DASH_FUSE1.2, DASH_FUSE1.7, DASH_FUSE1.8, FRONT_BATTERY_INHIBIT1.4, IGNITION_FUSE1.1, IGNITION_FUSE1.2, IGNITION_FUSE1.7, IGNITION_FUSE1.8, INVERTER_FUSE1.1, INVERTER_FUSE1.2, INVERTER_FUSE1.7, INVERTER_FUSE1.8, ISA_SHUNT_FUSE1.1, ISA_SHUNT_FUSE1.2, ISA_SHUNT_FUSE1.7, ISA_SHUNT_FUSE1.8, J1.2, J5.2, REAR_BATTERY_INHIBIT1.4
BRAKE_SIGNAL: J10.2, J11.1
BRAKE_SWITCH_SEND: BRAKE_FUSE1.3, BRAKE_FUSE1.4, BRAKE_FUSE1.5, BRAKE_FUSE1.6, J10.1
CHARGER_ENABLE_IN: D2.2 (A), D3.2 (A), J3.1
CHG_CONTACTORS_12V: CHARGING_CONTACTORS1.1, J12.1
CONTACTORS_12V: CONTACTORS_FUSE1.3, CONTACTORS_FUSE1.4, CONTACTORS_FUSE1.5, CONTACTORS_FUSE1.6, J4.3
CONTACTORS_GND: CHARGING_CONTACTORS1.5, COOLANT_PUMP_RELAY1.5, D5.1 (K), D6.1 (K), FWD_DRIVE_INHIBIT_RELAY1.5, IGNITION_RELAY1.5, INVERTER_RELAY1.5, J1.1, J2.4, J7.2, J8.3, REV_DRIVE_INHIBIT_RELAY1.5
COOLANT_12V: COOLANT_PUMP_RELAY1.1, J7.1
CRUISE_BUTTON_RETURN: J5.4, J11.2
CRUISE_BUTTON_SEND: CRUISE_FUSE1.3, CRUISE_FUSE1.4, CRUISE_FUSE1.5, CRUISE_FUSE1.6, J5.3
DASH_12V: DASH_FUSE1.3, DASH_FUSE1.4, DASH_FUSE1.5, DASH_FUSE1.6, J8.1
DRIVE_INHIBIT: D4.1 (K), FWD_DRIVE_INHIBIT_RELAY1.4, J3.4, REV_DRIVE_INHIBIT_RELAY1.4
FRONT_BATTERY_ENABLE: FRONT_BATTERY_INHIBIT1.2, J15.1
FRONT_BATTERY_INHIBIT: FRONT_BATTERY_INHIBIT1.5, J15.2
HVJB_GND: J4.4
IGNITION_12V: BRAKE_FUSE1.1, BRAKE_FUSE1.2, BRAKE_FUSE1.7, BRAKE_FUSE1.8, CONTACTORS_FUSE1.1, CONTACTORS_FUSE1.2, CONTACTORS_FUSE1.7, CONTACTORS_FUSE1.8, CRUISE_FUSE1.1, CRUISE_FUSE1.2, CRUISE_FUSE1.7, CRUISE_FUSE1.8, D1.2 (A), IGNITION_RELAY1.1, J4.1, J6.3, J8.4, J9.1, J9.2, J9.3, J9.4, R1.1, WIPER_FUSE1.1, WIPER_FUSE1.2, WIPER_FUSE1.7, WIPER_FUSE1.8
IGNITION_ENABLE_OUT: INVERTER_RELAY1.1, J2.2, J3.2
IGNITION_SWITCH_B: IGNITION_RELAY1.4, J5.1
INVERTER_FWD: FWD_DRIVE_INHIBIT_RELAY1.2, J2.3
INVERTER_REV: J2.1, J3.3, REV_DRIVE_INHIBIT_RELAY1.2
ISA_SHUNT_12V: ISA_SHUNT_FUSE1.3, ISA_SHUNT_FUSE1.4, ISA_SHUNT_FUSE1.5, ISA_SHUNT_FUSE1.6, J4.2
unnamed: CHARGING_CONTACTORS1.3, CHARGING_CONTACTORS_FUSE1.3, CHARGING_CONTACTORS_FUSE1.4, CHARGING_CONTACTORS_FUSE1.5, CHARGING_CONTACTORS_FUSE1.6
unnamed: COOLANT_PUMP_FUSE1.3, COOLANT_PUMP_FUSE1.4, COOLANT_PUMP_FUSE1.5, COOLANT_PUMP_FUSE1.6, COOLANT_PUMP_RELAY1.3
unnamed: COOLANT_PUMP_RELAY1.4, D1.1 (K), D2.1 (K), FRONT_BATTERY_INHIBIT1.3, INVERTER_RELAY1.4, REAR_BATTERY_INHIBIT1.3
unnamed: CHARGING_CONTACTORS1.4, D3.1 (K), D4.2 (A), R2.1
unnamed: D5.2 (A), R1.2
unnamed: D6.2 (A), R2.2
unnamed: IGNITION_FUSE1.3, IGNITION_FUSE1.4, IGNITION_FUSE1.5, IGNITION_FUSE1.6, IGNITION_RELAY1.3
unnamed: INVERTER_FUSE1.3, INVERTER_FUSE1.4, INVERTER_FUSE1.5, INVERTER_FUSE1.6, INVERTER_RELAY1.3
REAR_BATTERY_ENABLE: J14.1, REAR_BATTERY_INHIBIT1.2
REAR_BATTERY_INHIBIT: J14.2, REAR_BATTERY_INHIBIT1.5
SHIFTER_FWD: FWD_DRIVE_INHIBIT_RELAY1.3, J6.1
SHIFTER_REV: J6.4, REV_DRIVE_INHIBIT_RELAY1.3
WIPER_SWITCH_SEND: J8.2, WIPER_FUSE1.3, WIPER_FUSE1.4, WIPER_FUSE1.5, WIPER_FUSE1.6

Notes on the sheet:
INVERTER Gear selection signals to inverter
HVJB Power to charging contactors
IGNITION
Inhibit signals ->low side switch from BMS
BRAKE SW
BATTERY Direct feed from 12V Battery
relay 160ma relay 160ma
HVJB Power into HVJB
COOLANT PUMP
relay 160ma
BRAKE Brake switch
SHIFTER Signals to/from shifter switch
Enable signals -> 12V supply to battery box cotactors
Always on
contactor 120ma contactor 120ma
FRONT BATTERY
INVERTER Signals
Activated by ignition or charger
EXTRA IGN
1000ma
INPUTS/OUTPUTS
ISA
Battery box contactors
CONTACTORS Main Precharge
INVERTER
pos contactor 120ma neg contactor 120ma
REAR Signals to/from rear of car
DASH Ignition and cruise
DASH Dash power and signals
Activated by charger only
CHARGING CONTACTORS
0ma
CRUISE
REAR BATTERY
Just use contactor GND
DRIVE INHIBIT
160ma

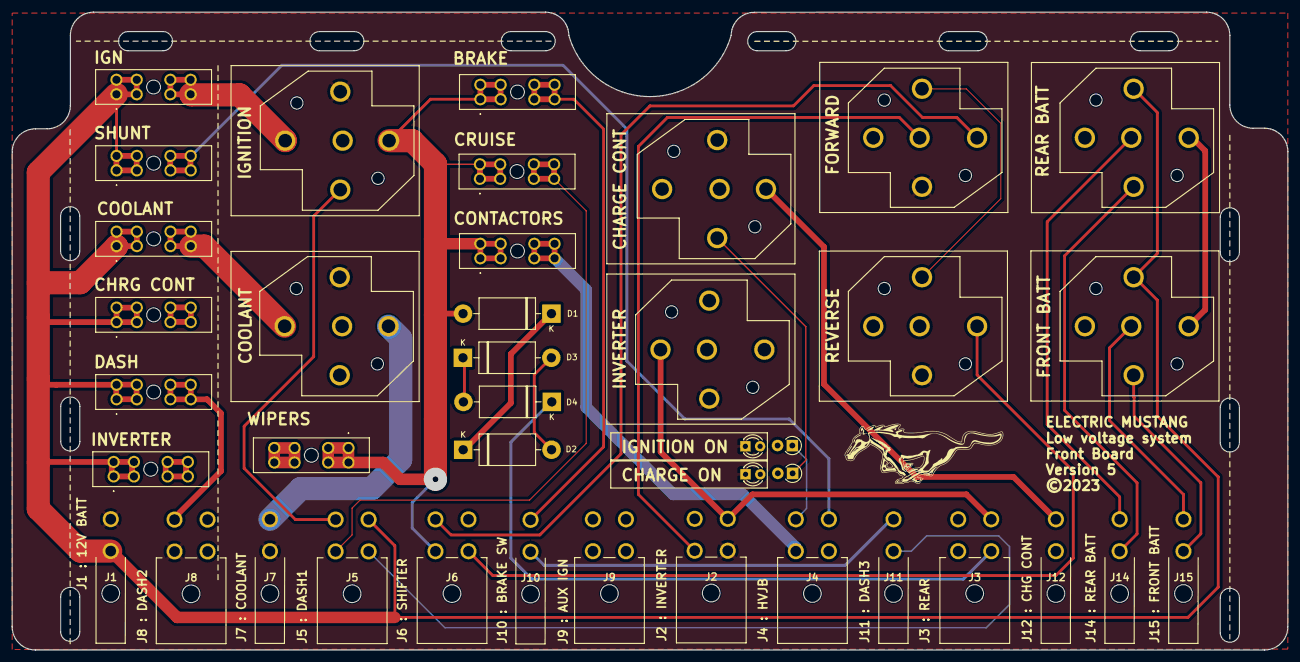
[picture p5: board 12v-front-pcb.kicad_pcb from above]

Board: 4 copper layers, 220.0 x 110.0 mm, 40 parts (0 on the bottom side), 33 nets.

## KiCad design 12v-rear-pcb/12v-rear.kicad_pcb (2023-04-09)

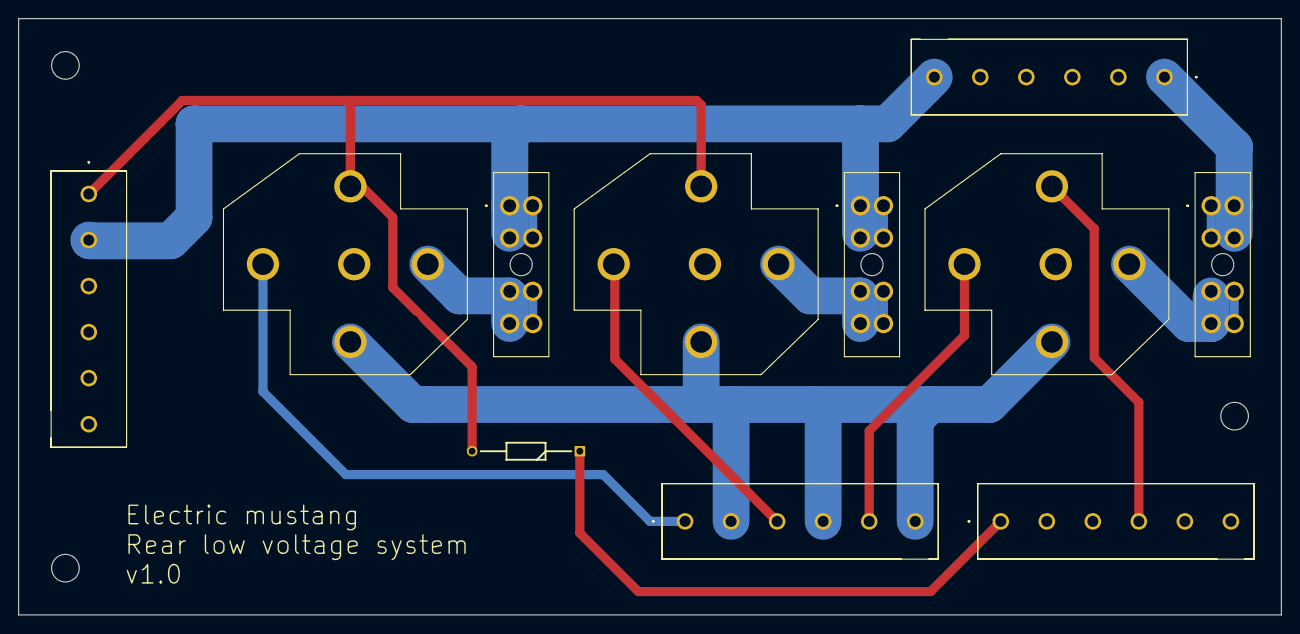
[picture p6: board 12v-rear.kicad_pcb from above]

Board: 2 copper layers, 137.2 x 64.8 mm, 14 parts (0 on the bottom side), 12 nets.

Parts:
D1: 10A10; DIOAD1165W56L425D185
FRONT_1, FRONT_2: 282836-6; 2828366
H1, H2, H3: MountingHole; MountingHole_3mm
LIM_FUSE1: 178.6165.0001; 17861650001
LIM_RELAY1: DZ85AB-5-PCB; DZ85AB5PCB
REAR_1, REAR_2: 282836-6; 2828366
REVERSE_LIGHT_FUSE1: 178.6165.0001; 17861650001
REVERSE_LIGHT_RELAY1: DZ85AB-5-PCB; DZ85AB5PCB
TESLA_FUSE1: 178.6165.0001; 17861650001
TESLA_RELAY1: DZ85AB-5-PCB; DZ85AB5PCB

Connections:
CHARGER_ON_SIGNAL: D1.1, FRONT_2.1
CHARGER_SWITCH_A: FRONT_1.6, LIM_FUSE1.1, LIM_FUSE1.2, LIM_FUSE1.7, LIM_FUSE1.8, REAR_2.2, TESLA_FUSE1.1, TESLA_FUSE1.2, TESLA_FUSE1.7, TESLA_FUSE1.8
CHARGER_SWITCH_B: D1.2, LIM_RELAY1.5, REAR_2.1, TESLA_RELAY1.5
GND: LIM_RELAY1.4, REAR_1.2, REAR_1.4, REAR_1.6, REVERSE_LIGHT_RELAY1.4, TESLA_RELAY1.4
IGNITION_12V: FRONT_1.1, REVERSE_LIGHT_FUSE1.1, REVERSE_LIGHT_FUSE1.2, REVERSE_LIGHT_FUSE1.7, REVERSE_LIGHT_FUSE1.8
LIM_12V: LIM_RELAY1.3, REAR_1.3
unnamed: LIM_FUSE1.3, LIM_FUSE1.4, LIM_FUSE1.5, LIM_FUSE1.6, LIM_RELAY1.1
unnamed: REVERSE_LIGHT_FUSE1.3, REVERSE_LIGHT_FUSE1.4, REVERSE_LIGHT_FUSE1.5, REVERSE_LIGHT_FUSE1.6, REVERSE_LIGHT_RELAY1.1
unnamed: TESLA_FUSE1.3, TESLA_FUSE1.4, TESLA_FUSE1.5, TESLA_FUSE1.6, TESLA_RELAY1.1
REVERSE_LIGHT: REAR_1.5, REVERSE_LIGHT_RELAY1.3
REVERSE_SIGNAL: FRONT_2.4, REVERSE_LIGHT_RELAY1.5
TESLA_12V: REAR_1.1, TESLA_RELAY1.3

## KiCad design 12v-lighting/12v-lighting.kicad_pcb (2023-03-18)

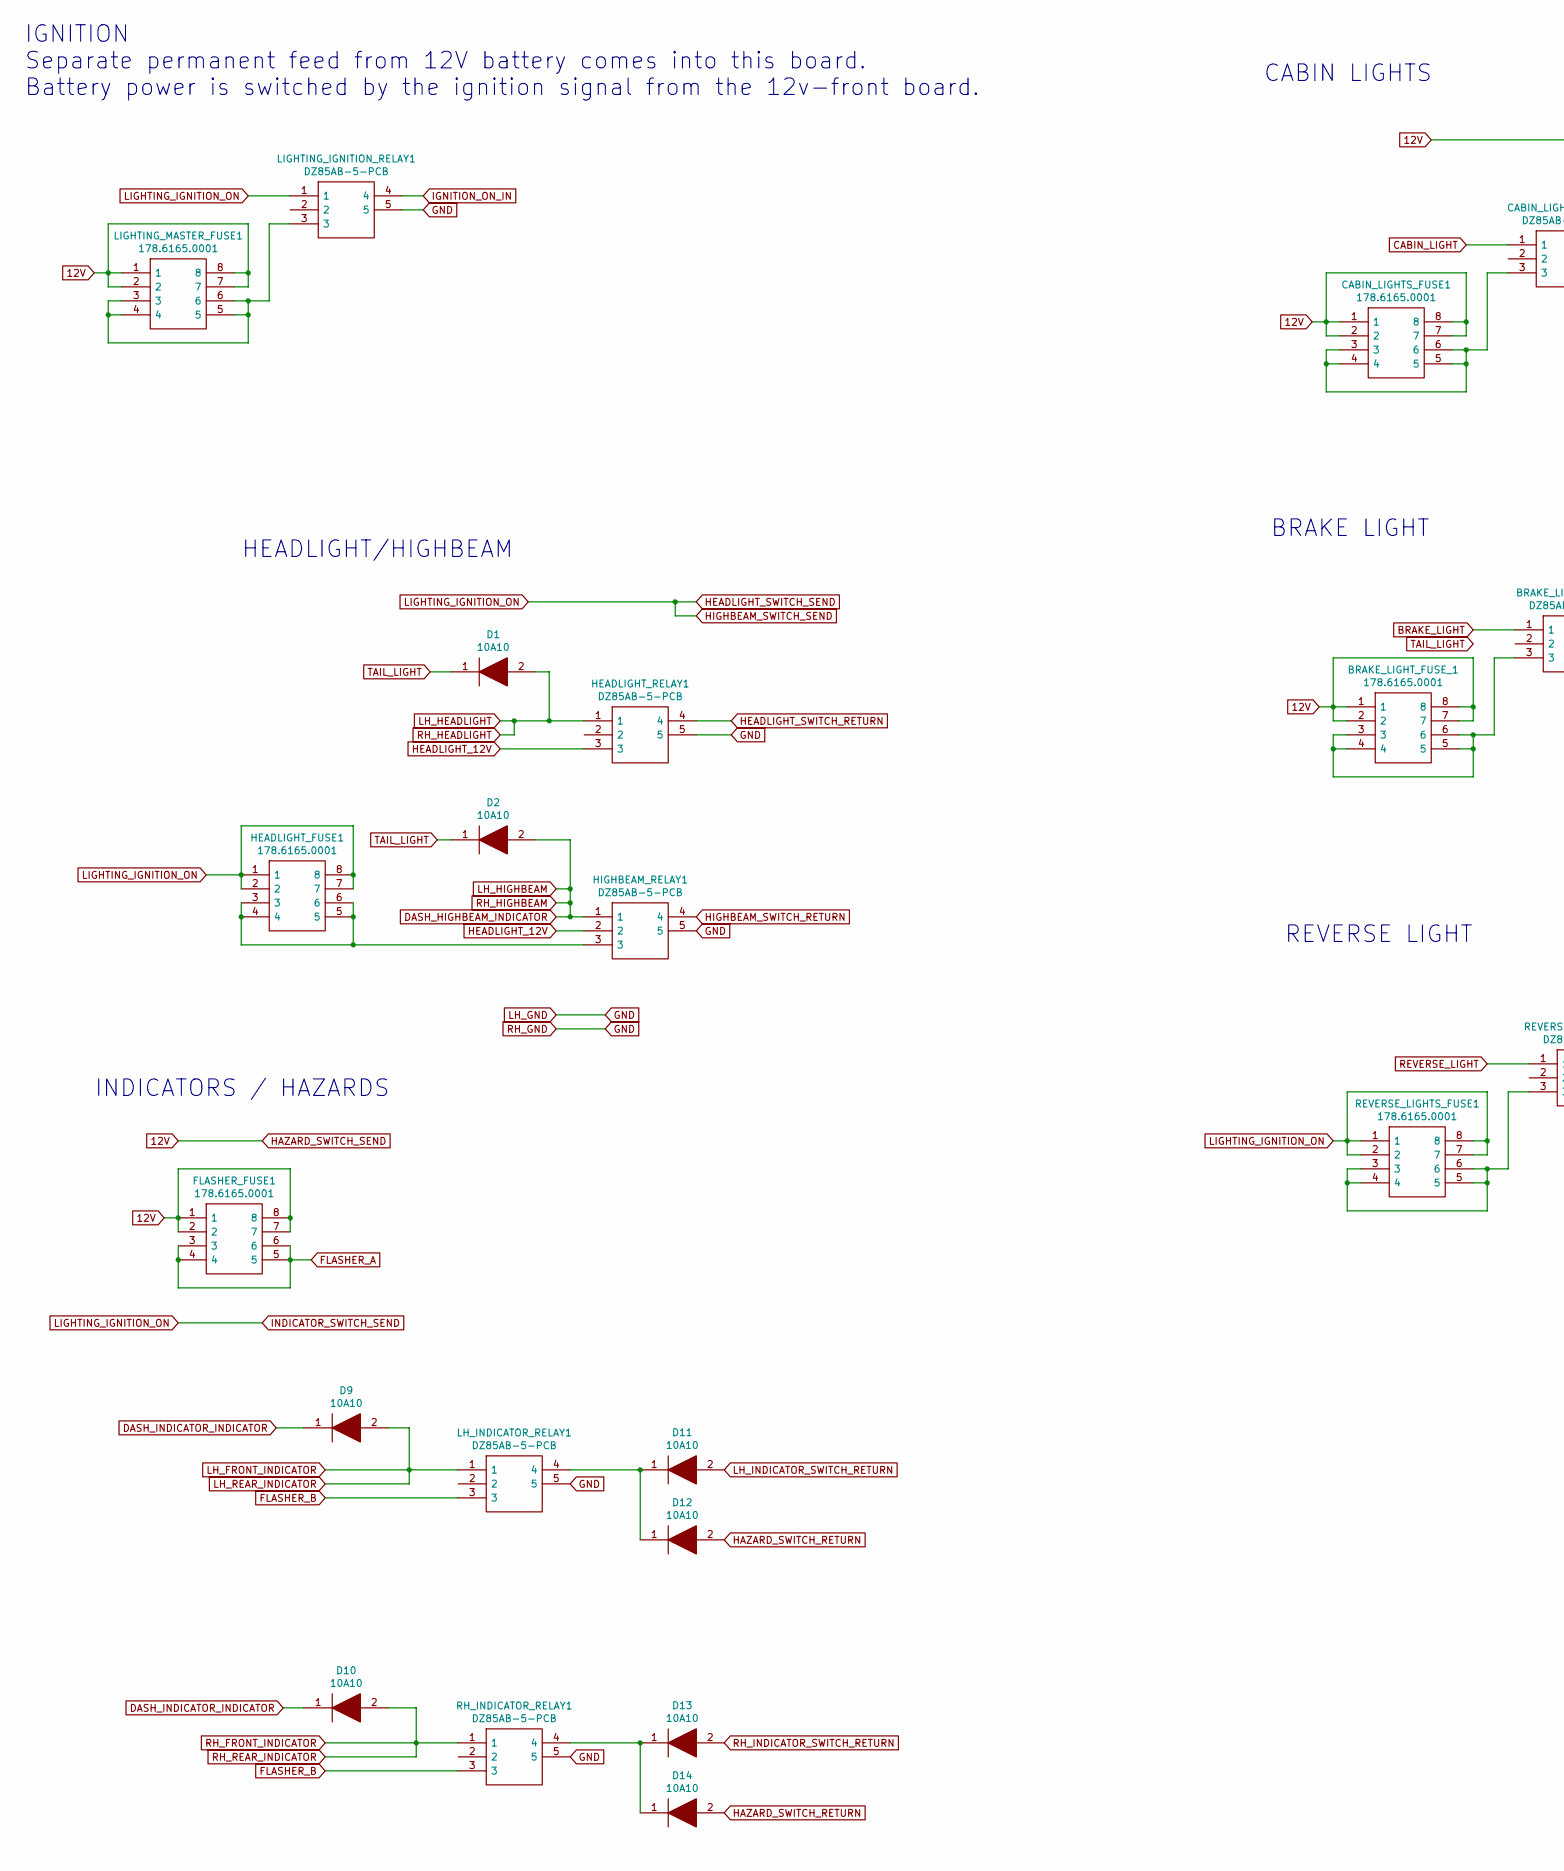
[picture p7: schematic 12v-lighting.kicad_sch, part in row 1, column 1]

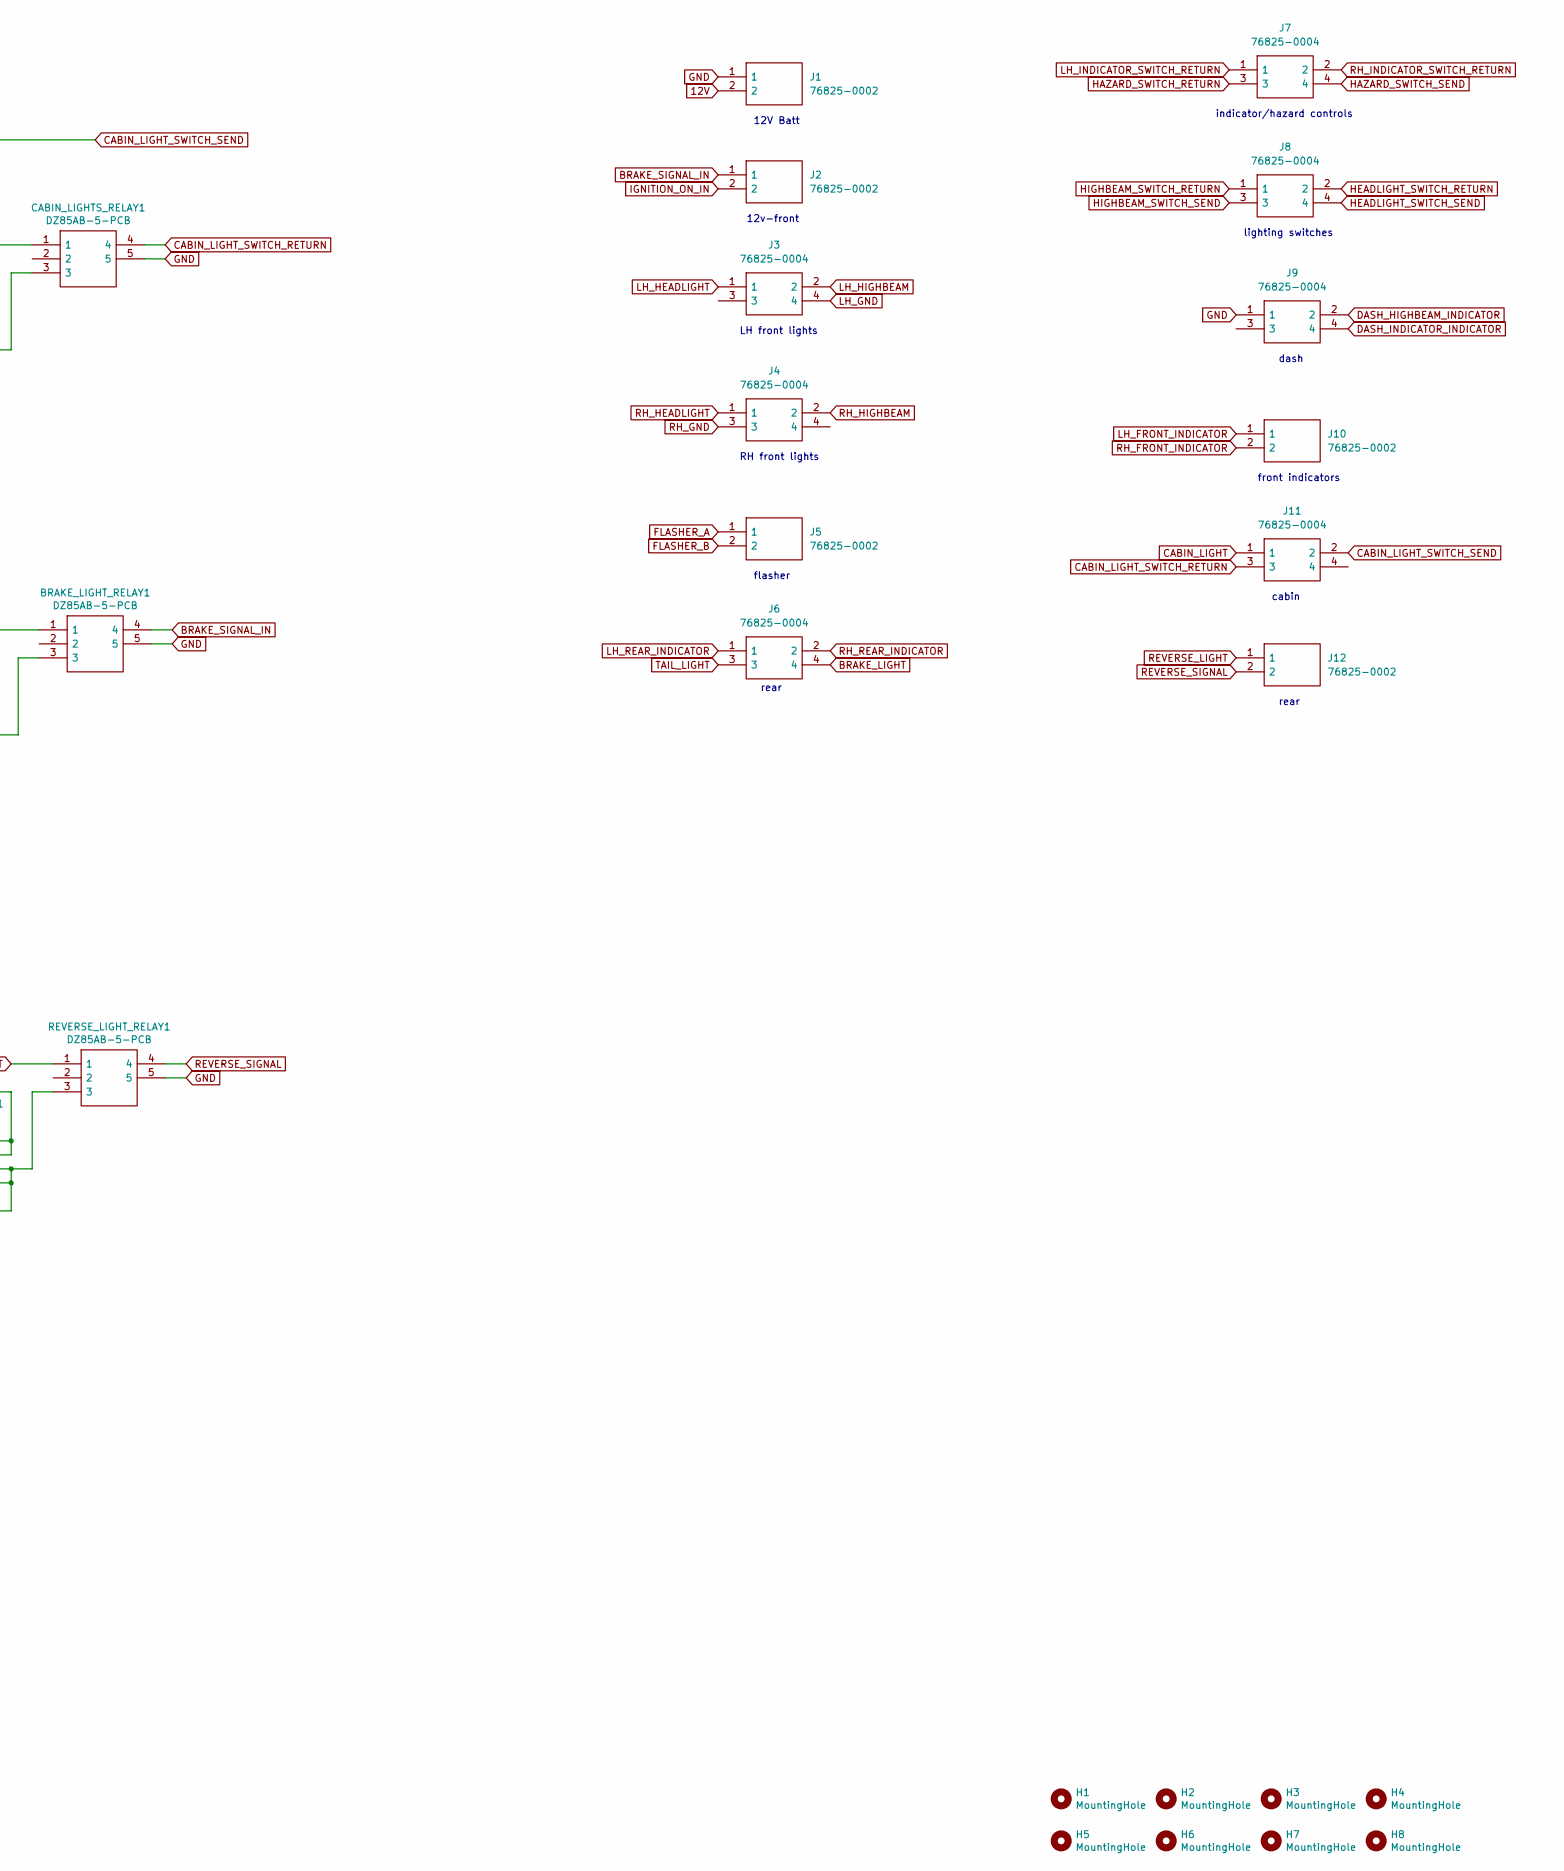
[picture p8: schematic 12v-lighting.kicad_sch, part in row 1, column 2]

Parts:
BRAKE_LIGHT_FUSE_1: 178.6165.0001; 17861650001; Manufacturer_Part_Number 178.6165.0001; Mouser Part Number 576-178.6165.0001
BRAKE_LIGHT_RELAY1: DZ85AB-5-PCB; DZ85AB5PCB; Manufacturer_Part_Number DZ85AB-5-PCB
CABIN_LIGHTS_FUSE1: 178.6165.0001; 17861650001; Manufacturer_Part_Number 178.6165.0001; Mouser Part Number 576-178.6165.0001
CABIN_LIGHTS_RELAY1: DZ85AB-5-PCB; DZ85AB5PCB; Manufacturer_Part_Number DZ85AB-5-PCB
D1, D2, D9, D10, D11, D12, D13, D14: 10A10; D_DO-201AD_P15.24mm_Horizontal; Manufacturer_Part_Number 10A10
FLASHER_FUSE1: 178.6165.0001; 17861650001; Manufacturer_Part_Number 178.6165.0001; Mouser Part Number 576-178.6165.0001
H1, H2, H3, H4, H5, H6, H7, H8: MountingHole; MountingHole_3.2mm_M3
HEADLIGHT_FUSE1: 178.6165.0001; 17861650001; Manufacturer_Part_Number 178.6165.0001; Mouser Part Number 576-178.6165.0001
HEADLIGHT_RELAY1: DZ85AB-5-PCB; DZ85AB5PCB; Manufacturer_Part_Number DZ85AB-5-PCB
HIGHBEAM_RELAY1: DZ85AB-5-PCB; DZ85AB5PCB; Manufacturer_Part_Number DZ85AB-5-PCB
J1, J2, J5, J10, J12: 76825-0002; 768250002; Manufacturer_Part_Number 76825-0002; Mouser Part Number 538-76825-0002
J3, J4, J6, J7, J8, J9, J11: 76825-0004; 768250004; Manufacturer_Part_Number 76825-0004; Mouser Part Number 538-76825-0004
LH_INDICATOR_RELAY1: DZ85AB-5-PCB; DZ85AB5PCB; Manufacturer_Part_Number DZ85AB-5-PCB
LIGHTING_IGNITION_RELAY1: DZ85AB-5-PCB; DZ85AB5PCB; Manufacturer_Part_Number DZ85AB-5-PCB
LIGHTING_MASTER_FUSE1: 178.6165.0001; 17861650001; Manufacturer_Part_Number 178.6165.0001; Mouser Part Number 576-178.6165.0001
REVERSE_LIGHTS_FUSE1: 178.6165.0001; 17861650001; Manufacturer_Part_Number 178.6165.0001; Mouser Part Number 576-178.6165.0001
REVERSE_LIGHT_RELAY1: DZ85AB-5-PCB; DZ85AB5PCB; Manufacturer_Part_Number DZ85AB-5-PCB
RH_INDICATOR_RELAY1: DZ85AB-5-PCB; DZ85AB5PCB; Manufacturer_Part_Number DZ85AB-5-PCB

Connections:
12V: BRAKE_LIGHT_FUSE_1.1, BRAKE_LIGHT_FUSE_1.2, BRAKE_LIGHT_FUSE_1.7, BRAKE_LIGHT_FUSE_1.8, CABIN_LIGHTS_FUSE1.1, CABIN_LIGHTS_FUSE1.2, CABIN_LIGHTS_FUSE1.7, CABIN_LIGHTS_FUSE1.8, FLASHER_FUSE1.1, FLASHER_FUSE1.2, FLASHER_FUSE1.7, FLASHER_FUSE1.8, J1.2, J7.4, J11.2, LIGHTING_MASTER_FUSE1.1, LIGHTING_MASTER_FUSE1.2, LIGHTING_MASTER_FUSE1.7, LIGHTING_MASTER_FUSE1.8
BRAKE_LIGHT: BRAKE_LIGHT_RELAY1.1, J6.4
BRAKE_SIGNAL_IN: BRAKE_LIGHT_RELAY1.4, J2.1
CABIN_LIGHT: CABIN_LIGHTS_RELAY1.1, J11.1
CABIN_LIGHT_SWITCH_RETURN: CABIN_LIGHTS_RELAY1.4, J11.3
DASH_HIGHBEAM_INDICATOR: D2.2, HIGHBEAM_RELAY1.1, J3.2, J4.2, J9.2
DASH_INDICATOR_INDICATOR: D9.1, D10.1, J9.4
FLASHER_A: FLASHER_FUSE1.3, FLASHER_FUSE1.4, FLASHER_FUSE1.5, FLASHER_FUSE1.6, J5.1
FLASHER_B: J5.2, LH_INDICATOR_RELAY1.3, RH_INDICATOR_RELAY1.3
GND: BRAKE_LIGHT_RELAY1.5, CABIN_LIGHTS_RELAY1.5, HEADLIGHT_RELAY1.5, HIGHBEAM_RELAY1.5, J1.1, J3.4, J4.3, J9.1, LH_INDICATOR_RELAY1.5, LIGHTING_IGNITION_RELAY1.5, REVERSE_LIGHT_RELAY1.5, RH_INDICATOR_RELAY1.5
HAZARD_SWITCH_RETURN: D12.2, D14.2, J7.3
HEADLIGHT_12V: HEADLIGHT_RELAY1.3, HIGHBEAM_RELAY1.2
HEADLIGHT_SWITCH_RETURN: HEADLIGHT_RELAY1.4, J8.2
HEADLIGHT_SWITCH_SEND: HEADLIGHT_FUSE1.1, HEADLIGHT_FUSE1.2, HEADLIGHT_FUSE1.7, HEADLIGHT_FUSE1.8, J8.3, J8.4, LIGHTING_IGNITION_RELAY1.1, REVERSE_LIGHTS_FUSE1.1, REVERSE_LIGHTS_FUSE1.2, REVERSE_LIGHTS_FUSE1.7, REVERSE_LIGHTS_FUSE1.8
HIGHBEAM_SWITCH_RETURN: HIGHBEAM_RELAY1.4, J8.1
IGNITION_ON_IN: J2.2, LIGHTING_IGNITION_RELAY1.4
LH_FRONT_INDICATOR: D9.2, J6.1, J10.1, LH_INDICATOR_RELAY1.1
LH_HEADLIGHT: D1.2, HEADLIGHT_RELAY1.1, J3.1, J4.1
LH_INDICATOR_SWITCH_RETURN: D11.2, J7.1
unnamed: BRAKE_LIGHT_FUSE_1.3, BRAKE_LIGHT_FUSE_1.4, BRAKE_LIGHT_FUSE_1.5, BRAKE_LIGHT_FUSE_1.6, BRAKE_LIGHT_RELAY1.3
unnamed: CABIN_LIGHTS_FUSE1.3, CABIN_LIGHTS_FUSE1.4, CABIN_LIGHTS_FUSE1.5, CABIN_LIGHTS_FUSE1.6, CABIN_LIGHTS_RELAY1.3
unnamed: D11.1, D12.1, LH_INDICATOR_RELAY1.4
unnamed: D13.1, D14.1, RH_INDICATOR_RELAY1.4
unnamed: HEADLIGHT_FUSE1.3, HEADLIGHT_FUSE1.4, HEADLIGHT_FUSE1.5, HEADLIGHT_FUSE1.6, HIGHBEAM_RELAY1.3
unnamed: LIGHTING_IGNITION_RELAY1.3, LIGHTING_MASTER_FUSE1.3, LIGHTING_MASTER_FUSE1.4, LIGHTING_MASTER_FUSE1.5, LIGHTING_MASTER_FUSE1.6
unnamed: REVERSE_LIGHTS_FUSE1.3, REVERSE_LIGHTS_FUSE1.4, REVERSE_LIGHTS_FUSE1.5, REVERSE_LIGHTS_FUSE1.6, REVERSE_LIGHT_RELAY1.3
REVERSE_LIGHT: J12.1, REVERSE_LIGHT_RELAY1.1
REVERSE_SIGNAL: J12.2, REVERSE_LIGHT_RELAY1.4
RH_FRONT_INDICATOR: D10.2, J6.2, J10.2, RH_INDICATOR_RELAY1.1
RH_INDICATOR_SWITCH_RETURN: D13.2, J7.2
TAIL_LIGHT: D1.1, D2.1, J6.3

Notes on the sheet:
front indicators
lighting switches
RH front lights
12v-front
dash
LH front lights
REVERSE LIGHT
rear
HEADLIGHT/HIGHBEAM
CABIN LIGHTS
12V Batt
INDICATORS / HAZARDS
cabin
BRAKE LIGHT
flasher
IGNITION Separate permanent feed from 12V battery comes into this board. Battery power is switched by the ignition signal from the 12v-front board.
indicator/hazard controls

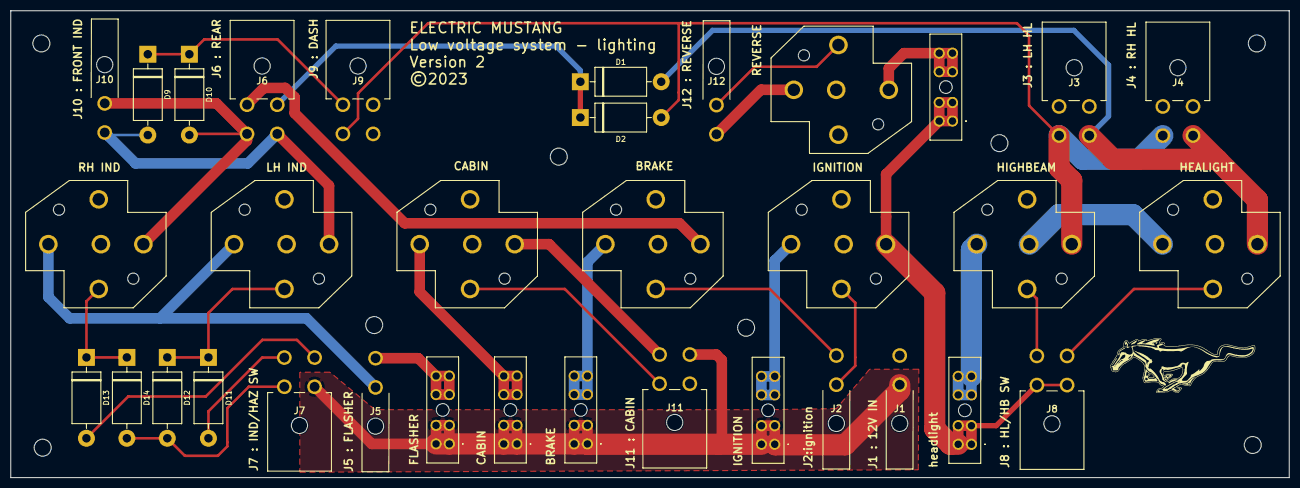
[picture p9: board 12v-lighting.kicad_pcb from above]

Board: 2 copper layers, 241.0 x 88.0 mm, 42 parts (0 on the bottom side), 31 nets.

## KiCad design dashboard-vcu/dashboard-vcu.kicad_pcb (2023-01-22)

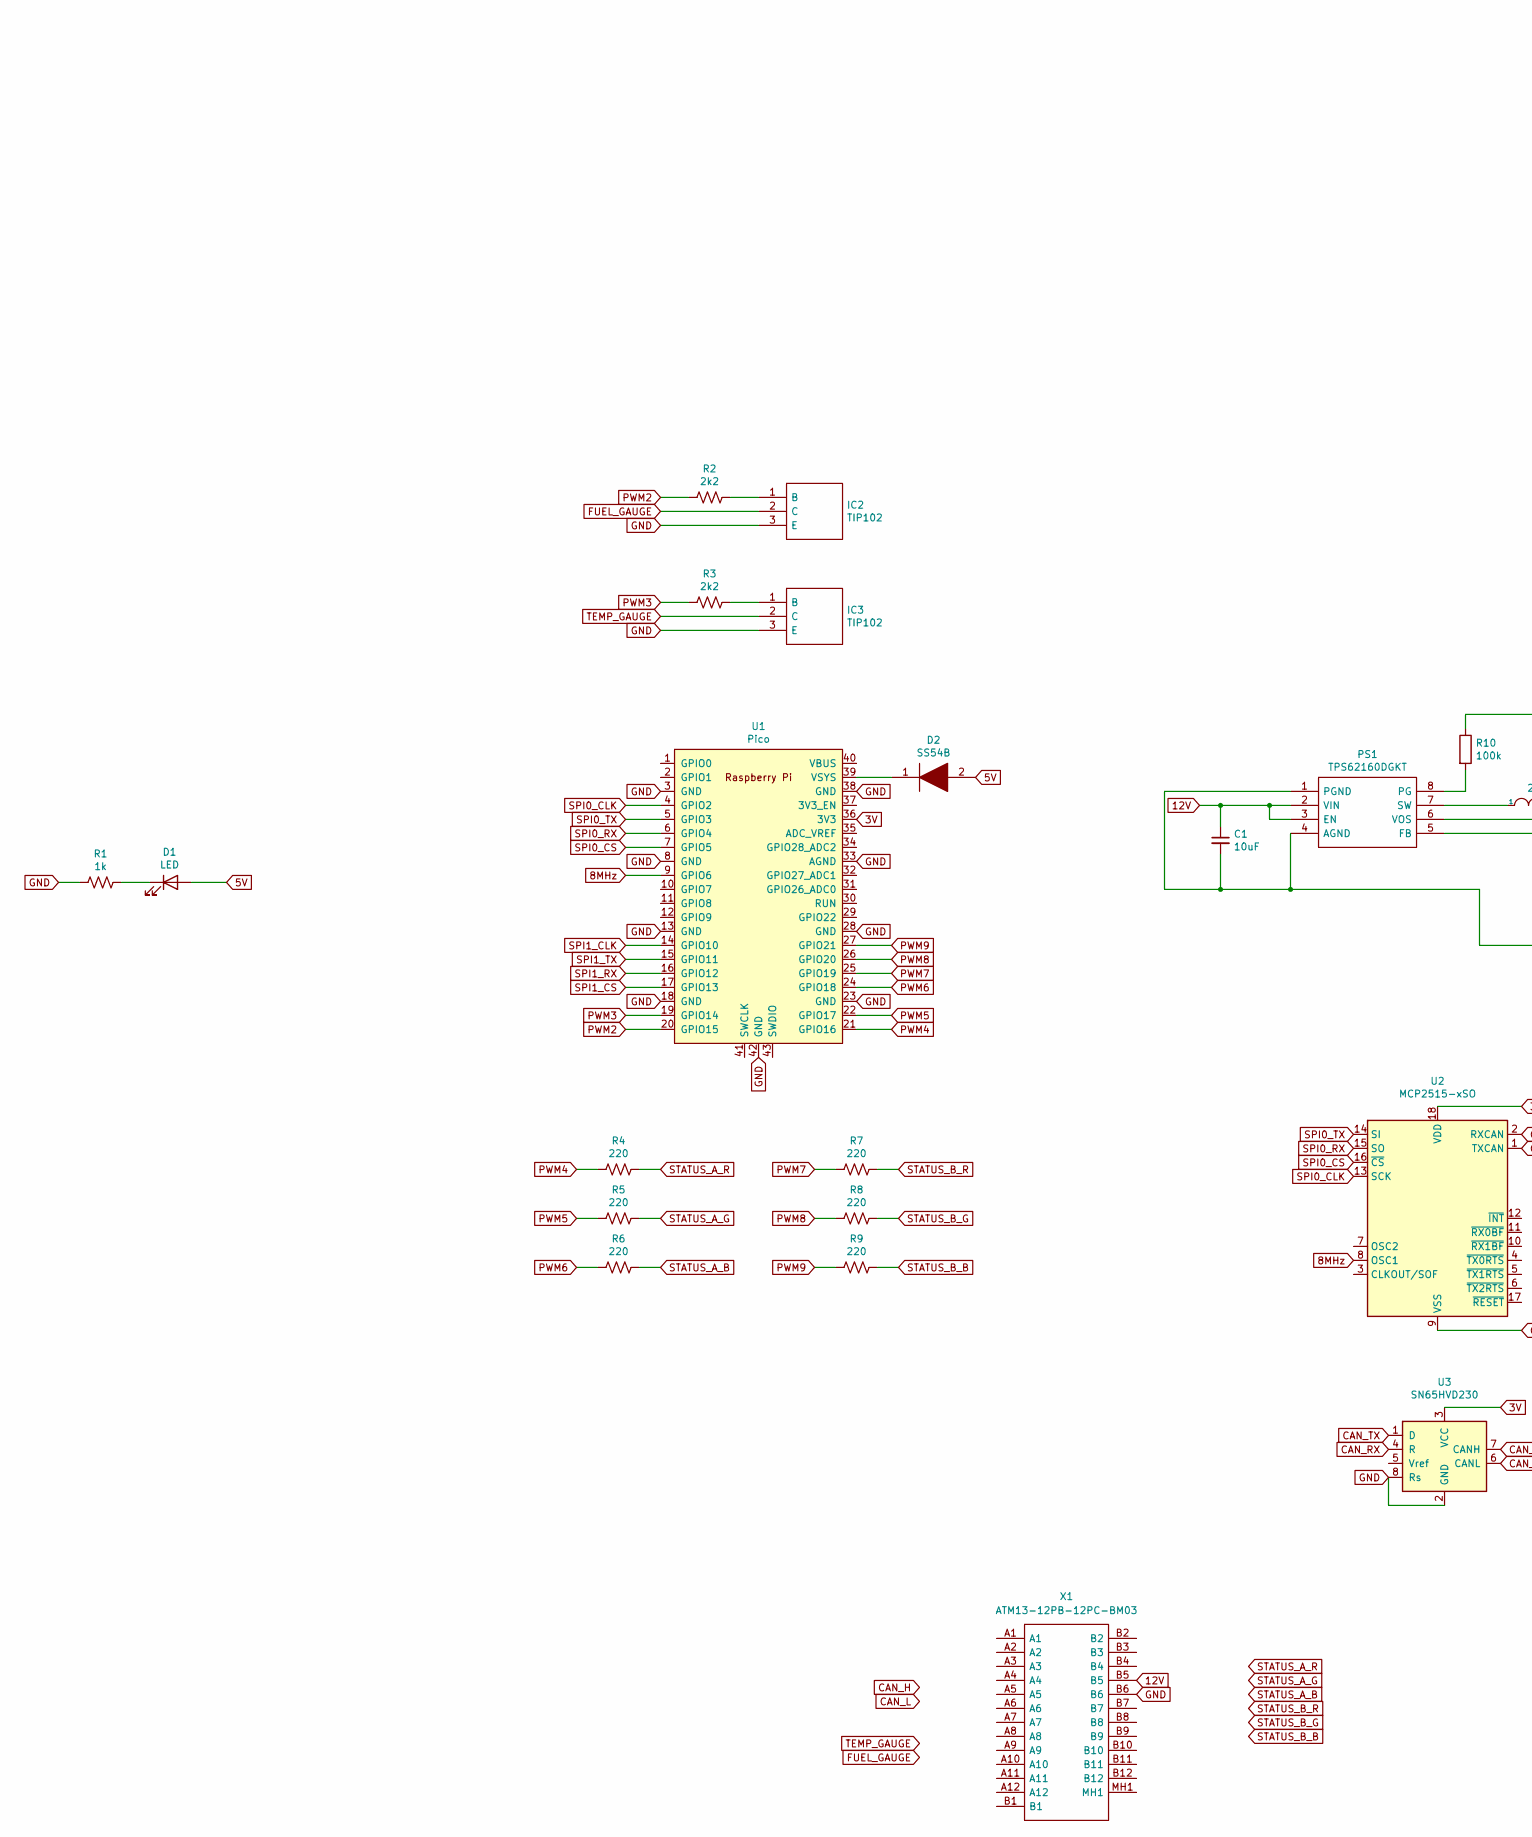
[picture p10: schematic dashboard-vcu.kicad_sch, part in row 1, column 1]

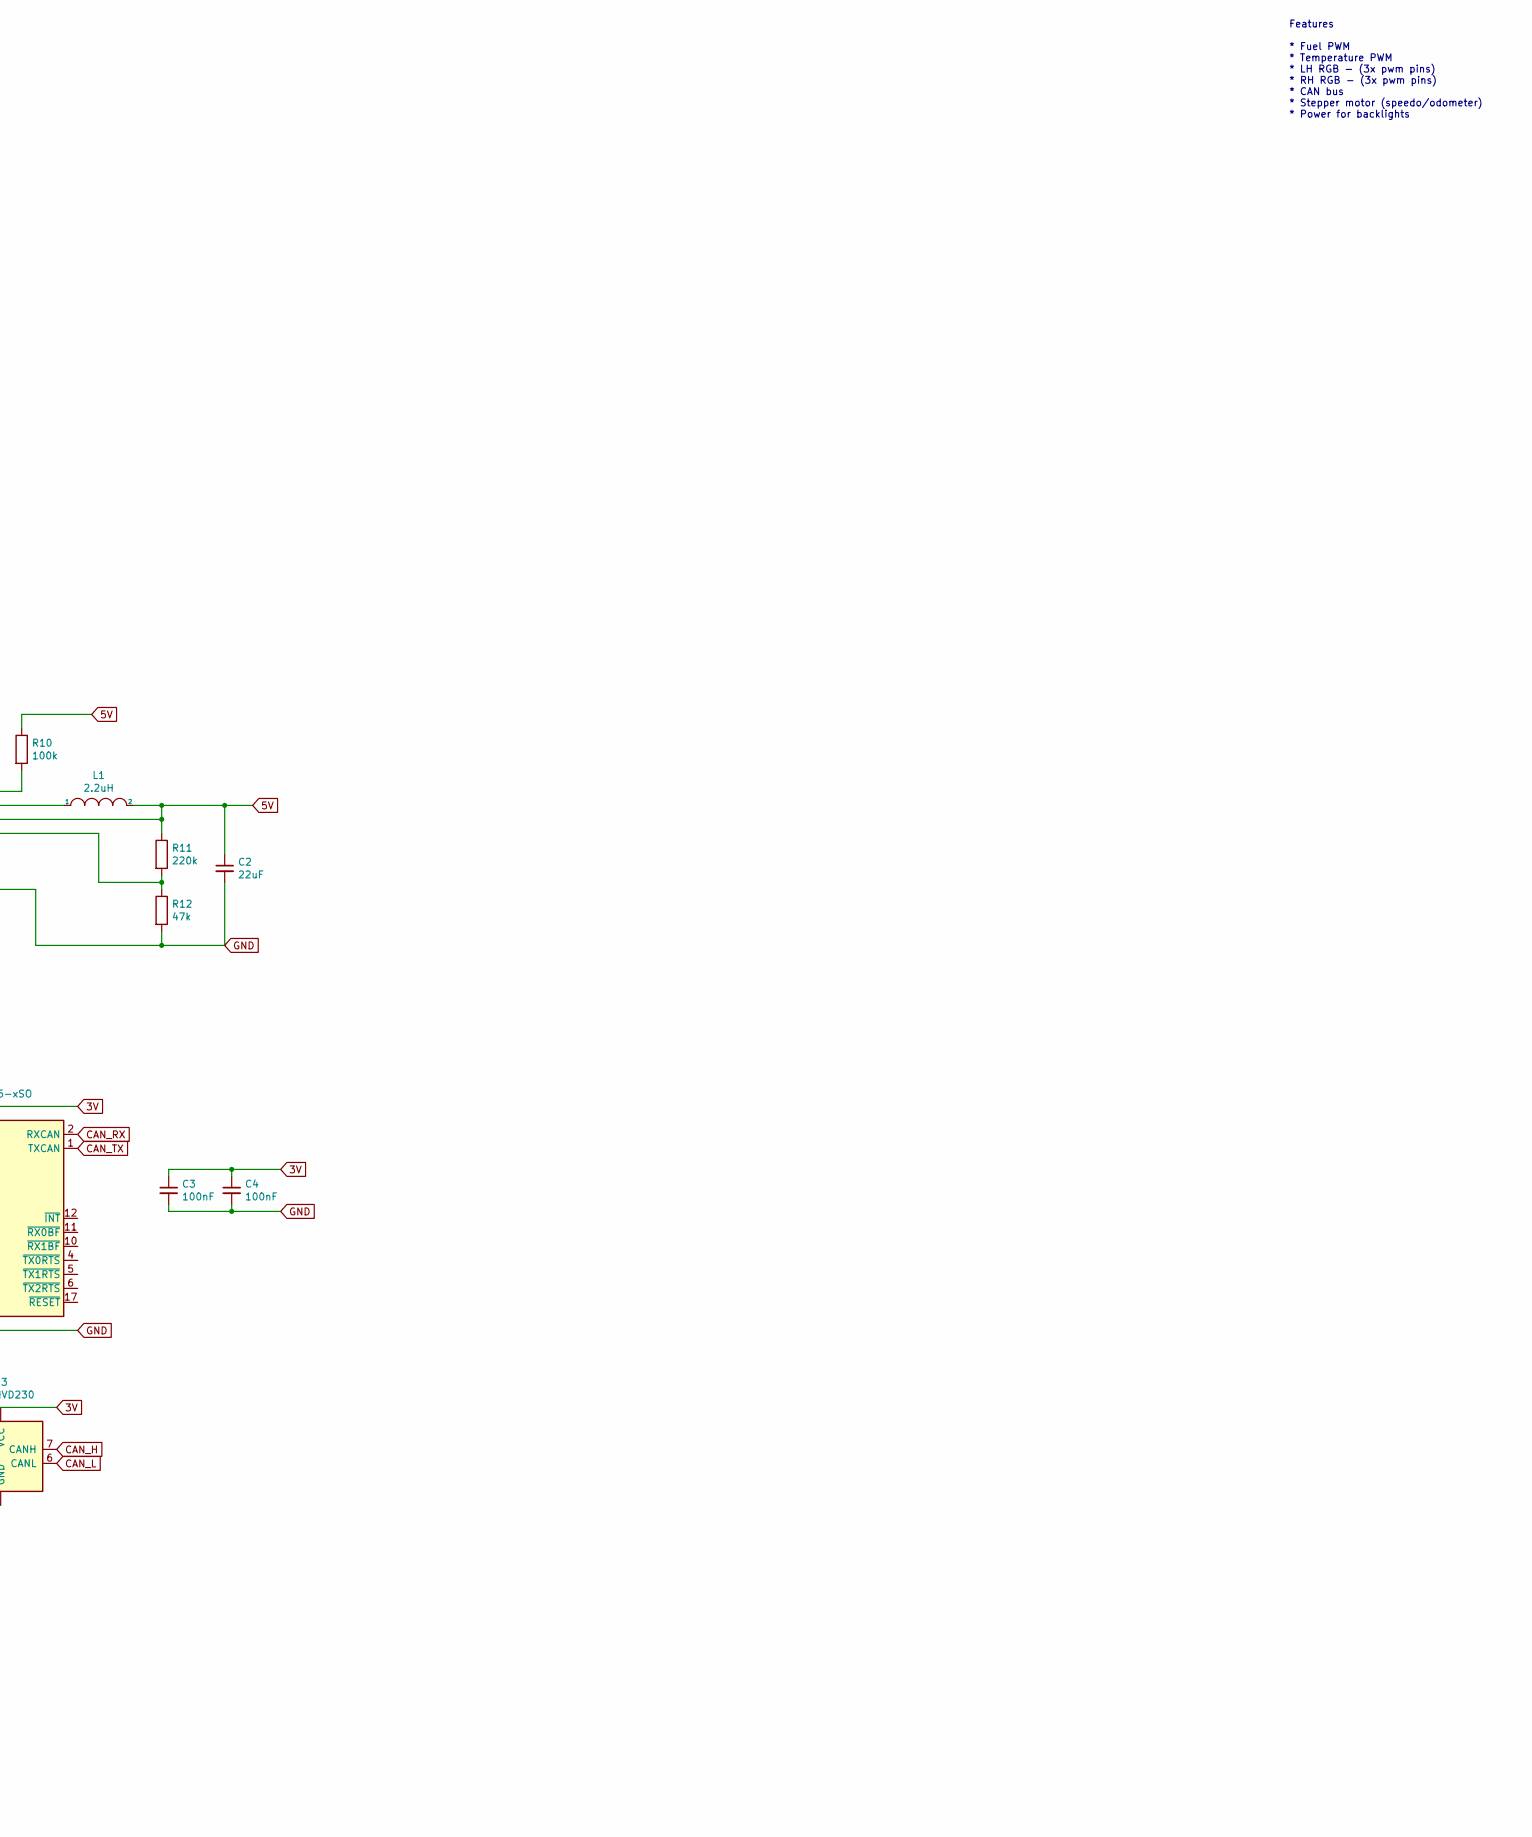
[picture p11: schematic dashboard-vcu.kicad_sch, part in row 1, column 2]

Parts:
C1: 10uF; C_0603_1608Metric
C2: 22uF; C_0805_2012Metric
C3, C4: 100nF; C_0603_1608Metric
D1: LED; LED_0603_1608Metric
D2: SS54B; DIOM5336X244N; Manufacturer_Part_Number SS54B
IC2, IC3: TIP102; TO270P460X1020X2008-3P; Manufacturer_Part_Number TIP102; Mouser Part Number 511-TIP102
L1: 2.2uH; NR6028T220M
PS1: TPS62160DGKT; SOP65P490X110-8N; Manufacturer_Part_Number TPS62160DGKT; Mouser Part Number 595-TPS62160DGKT
R1: 1k; R_0201_0603Metric
R2, R3: 2k2; R_0201_0603Metric
R4, R5, R6, R7, R8, R9: 220; R_0201_0603Metric
R10: 100k; R_0201_0603Metric
R11: 220k; R_0201_0603Metric
R12: 47k; R_0201_0603Metric
U1: Pico; RPi_Pico_SMD_TH
U2: MCP2515-xSO; SOIC-18W_7.5x11.6mm_P1.27mm
U3: SN65HVD230; SOIC-8_3.9x4.9mm_P1.27mm
X1: ATM13-12PB-12PC-BM03; ATM1312PB12PCBM03; Manufacturer_Part_Number ATM13-12PB-12PC-BM03; Mouser Part Number 654-ATM1312B12PCBM03

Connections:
3V: C3.1, C4.1, U1.36 (3V3), U2.18 (VDD), U3.3 (VCC)
5V: C2.1, D1.2 (A), D2.2, L1.2, PS1.6 (VOS), R10.1, R11.1
8MHz: U1.9 (GPIO6), U2.8 (OSC1)
12V: C1.1, PS1.2 (VIN), PS1.3 (EN), X1.B5
CAN_H: U3.7 (CANH)
CAN_L: U3.6 (CANL)
CAN_RX: U2.2 (RXCAN), U3.4 (R)
CAN_TX: U2.1 (TXCAN), U3.1 (D)
FUEL_GAUGE: IC2.2 (C)
GND: C1.2, C2.2, C3.2, C4.2, IC2.3 (E), IC3.3 (E), PS1.1 (PGND), PS1.4 (AGND), R1.2, R12.2, U1.3 (GND), U1.8 (GND), U1.13 (GND), U1.18 (GND), U1.23 (GND), U1.28 (GND), U1.33 (AGND), U1.38 (GND), U1.42 (GND), U2.9 (VSS), U3.2 (GND), U3.8 (Rs), X1.B6
unnamed: D1.1 (K), R1.1
unnamed: D2.1, U1.39 (VSYS)
unnamed: IC2.1 (B), R2.1
unnamed: IC3.1 (B), R3.1
unnamed: L1.1, PS1.7 (SW)
unnamed: PS1.5 (FB), R11.2, R12.1
unnamed: PS1.8 (PG), R10.2
PWM2: R2.2, U1.20 (GPIO15)
PWM3: R3.2, U1.19 (GPIO14)
PWM4: R4.2, U1.21 (GPIO16)
PWM5: R5.2, U1.22 (GPIO17)
PWM6: R6.2, U1.24 (GPIO18)
PWM7: R7.2, U1.25 (GPIO19)
PWM8: R8.2, U1.26 (GPIO20)
PWM9: R9.2, U1.27 (GPIO21)
SPI0_CLK: U1.4 (GPIO2), U2.13 (SCK)
SPI0_CS: U1.7 (GPIO5), U2.16 (~CS)
SPI0_RX: U1.6 (GPIO4), U2.15 (SO)
SPI0_TX: U1.5 (GPIO3), U2.14 (SI)
SPI1_CLK: U1.14 (GPIO10)
SPI1_CS: U1.17 (GPIO13)
SPI1_RX: U1.16 (GPIO12)
SPI1_TX: U1.15 (GPIO11)
STATUS_A_B: R6.1
STATUS_A_G: R5.1
STATUS_A_R: R4.1
STATUS_B_B: R9.1
STATUS_B_G: R8.1
STATUS_B_R: R7.1
TEMP_GAUGE: IC3.2 (C)

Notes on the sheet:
Features * Fuel PWM * Temperature PWM * LH RGB - (3x pwm pins) * RH RGB - (3x pwm pins) * CAN bus * Stepper motor (speedo/odometer) * Power for backlights

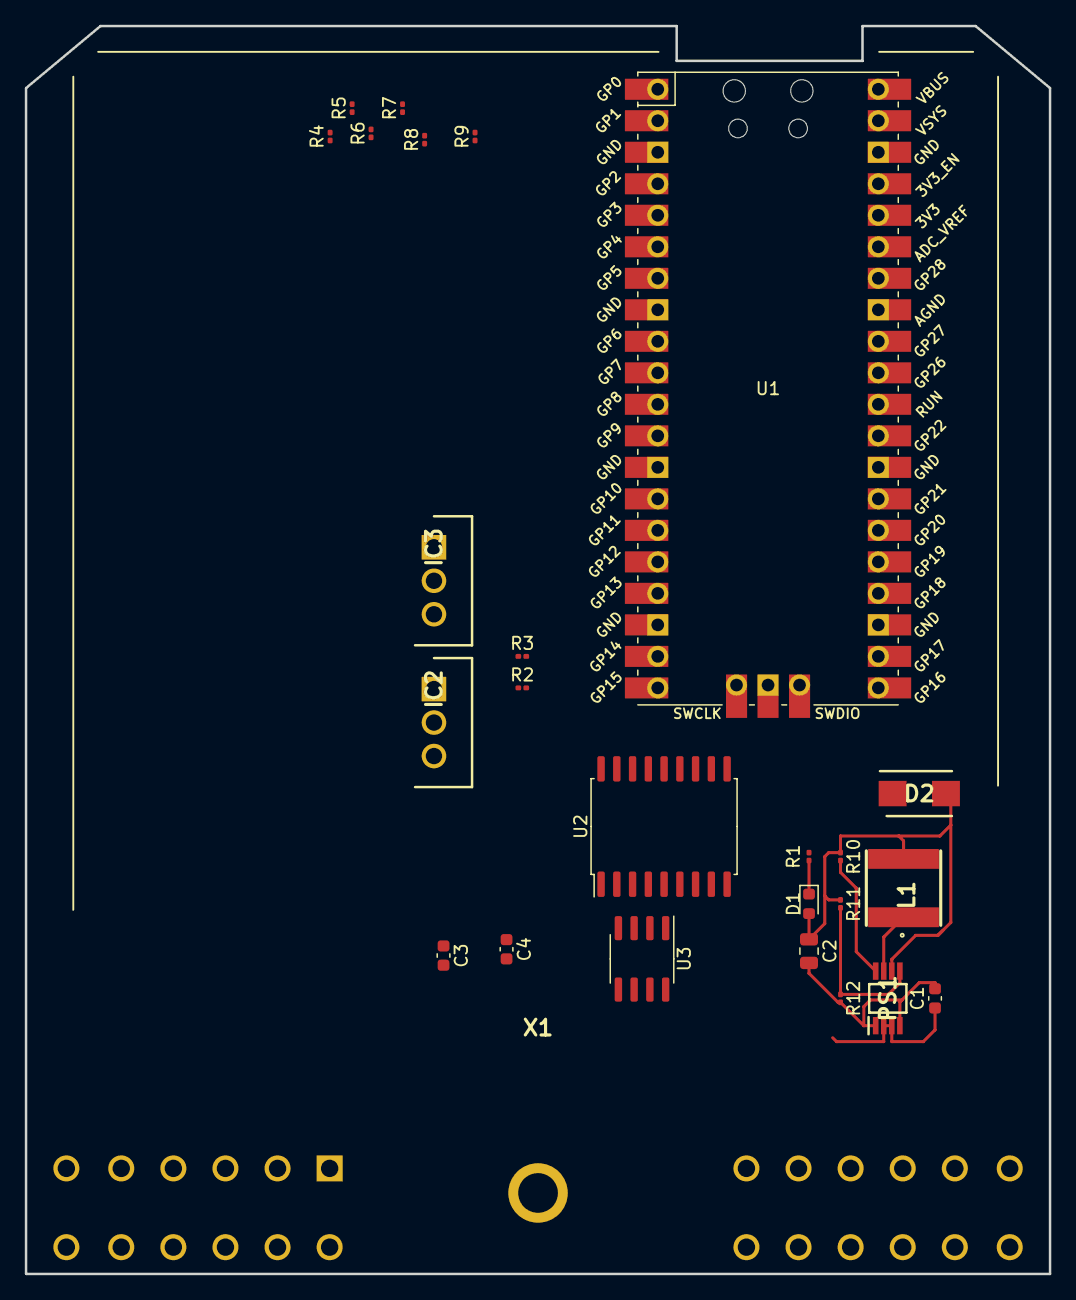
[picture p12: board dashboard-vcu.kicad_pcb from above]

Board: 2 copper layers, 82.6 x 100.6 mm, 26 parts (0 on the bottom side), 26 nets.

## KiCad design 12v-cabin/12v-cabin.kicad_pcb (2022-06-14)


Board: 2 copper layers, 8 parts (0 on the bottom side), 6 nets, no tracks yet.

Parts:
DASHBOARD_FUSE1: 178.6165.0001; 17861650001
H1, H2, H3, H4: MountingHole; MountingHole_3mm
HEATER_FAN_FUSE1: 178.6165.0001; 17861650001
HORN_FUSE1: 178.6165.0001; 17861650001
RADIO_FUSE1: 178.6165.0001; 17861650001

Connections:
DASHBOARD_12V: DASHBOARD_FUSE1.3, DASHBOARD_FUSE1.4, DASHBOARD_FUSE1.5, DASHBOARD_FUSE1.6
HEATER_FAN_12V: HEATER_FAN_FUSE1.3, HEATER_FAN_FUSE1.4, HEATER_FAN_FUSE1.5, HEATER_FAN_FUSE1.6
HORN_SWITCH_A: HEATER_FAN_FUSE1.1, HEATER_FAN_FUSE1.2, HEATER_FAN_FUSE1.7, HEATER_FAN_FUSE1.8, HORN_FUSE1.1, HORN_FUSE1.2, HORN_FUSE1.7, HORN_FUSE1.8
unnamed: HORN_FUSE1.3, HORN_FUSE1.4, HORN_FUSE1.5, HORN_FUSE1.6
unnamed: RADIO_FUSE1.3, RADIO_FUSE1.4, RADIO_FUSE1.5, RADIO_FUSE1.6
PERM_12V: DASHBOARD_FUSE1.1, DASHBOARD_FUSE1.2, DASHBOARD_FUSE1.7, DASHBOARD_FUSE1.8, RADIO_FUSE1.1, RADIO_FUSE1.2, RADIO_FUSE1.7, RADIO_FUSE1.8

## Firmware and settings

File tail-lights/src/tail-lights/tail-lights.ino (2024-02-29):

/*
 * This file is part of the ev mustang project.
 *
 * Copyright (C) 2023 Christian Kelly <chrskly@chrskly.com>
 *
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
 * You should have received a copy of the GNU General Public License
 * along with this program.  If not, see <http://www.gnu.org/licenses/>.
 */

#include "state.h"
#include "settings.h"

State state = OFF;

unsigned long flashPoint;
unsigned long previousFlashPoint;

void setup() {

}



void loop() {

/*
    // FLASH overrides everything else
    if ( digitalRead(FLASH_IN_PIN) == 1 ) {
        if ( state != FLASH ) {
            flashPoint = 0;
        }
        do_flash();
    }

    // 
    else if ( digitalRead(BRAKE_IN_PIN) == 1 ) {
        do_brake();
    }

    // Car lights are on, do running lights
    else if ( digitalRead(LIGHTS_ON_IN_PIN) == 1 ) {
        do_lights();
    }

    // Off
    else {
        do_off();
    }
*/

    do_flash();

}

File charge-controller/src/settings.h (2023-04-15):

/*
 * This file is part of the ev mustang charge controller project.
 *
 * Copyright (C) 2022 Christian Kelly <chrskly@chrskly.com>
 *
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
 * You should have received a copy of the GNU General Public License
 * along with this program.  If not, see <http://www.gnu.org/licenses/>.
 */

#ifndef SETTINGS_H
#define SETTINGS_H

#define VERSION 1.0

// Serial port
#define UART_ID      uart0
#define BAUD_RATE   115200
#define UART_TX_PIN      0 // pin 1
#define UART_RX_PIN      1 // pin 2

// SPI
#define SPI_PORT      spi0
#define SPI_MISO        16 // pin 21
#define SPI_CLK         18 // pin 24
#define SPI_MOSI        19 // pin 25
#define CAN_CLK_PIN     21 // pin 27

#define MAIN_CAN_CS     17
#define CHADEMO_CAN_CS  15
#define CCS_CAN_CS      20

#define CHARGE_INHIBIT_PIN 99

// Chademo pins
#define CHADEMO_IN1_PIN 99  // CP  - contactor +ve, (sensed by 'f'), d1 enable signal, chademo plug pin 2
#define CHADEMO_IN2_PIN 99  // CP2 - contactor -ve, (sensed by 'g'), d2 enable signal, chademo plug pin 10
#define CHADEMO_OUT1_PIN 99 // CP3 - charge enable, (switched by 'k'), chademo plug pin 4
#define CHADEMO_OUT2_PIN 99 // contactor relay control, 'e'

#define CHADEMO_CS_PIN 99   // CS - pilot wire, input, (a.k.a 'h'), pilot signal, chademo plug pin 7

// Version of ChaDeMo protocol to use. 1 == v0.9, 2 == v1.0
#define CHADEMO_PROTOCOL_VERSION 1

// Messages from ChaDeMo station
#define EVSE_CAPABILITIES_MESSAGE_ID 0x108
#define EVSE_STATUS_MESSAGE_ID 0x109

// Spec says current requests from the car should only vary at a rate of +/- 20A/sec
#define CHADEMO_RAMP_RATE 20
#define CHADEMO_RAMP_INTERVAL 1000 // units = ms

// Messages from BMS

// max/min pack voltage, max dis/charge current
#define BMS_LIMITS_MESSAGE_ID 0x351

// soc
#define BMS_SOC_MESSAGE_ID 0x355

// pack voltage, current (not implemented), temp
#define BMS_STATUS_MESSAGE_ID 0x356

// Alarms/warnings from BMS
#define BMS_ALARM_MESSAGE_ID 0x35A

// If we don't see the BMS in this number of seconds, then something is wrong
#define BMS_TTL 5

// If we don't see the ChaDeMo station in this number of seconds, then something is wrong
#define CHADEMO_STATION_TTL 2

// This scaling factor is used to calculate max charging time from the estimated charging time
#define MAX_CHARGING_TIME_SCALING_FACTOR 1.2

//
// Battery settings
//

#define BATTERY_MAX_VOLTAGE 350         // fixme put in proper value

// The SoC at which to stop fast-charging. Can be overriden via CAN msg.
#define BATTERY_FAST_CHARGE_DEFAULT_SOC_MAX 80

#define BATTERY_MAX_CURRENT 10          // fixme put in proper value
#define BATTERY_MAX_CURRENT_FAILSAFE 10 // maximum current to use if we lose communication with the BMS

#endif

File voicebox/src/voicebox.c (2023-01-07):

#include <stdio.h>
#include "pico/stdlib.h"
#include "hardware/dma.h"
#include "hardware/irq.h"
#include "hardware/pwm.h"
#include "hardware/sync.h"
#include "hardware/adc.h"

#define AUDIO_PIN 2
#define ADC_CHANNEL 2

//#define AUDIO_SAMPLES 62294
#define AUDIO_SAMPLES 2560

//#include "rock.h"

// 130MHz

int cur_sample = 0;
int EngineRpm = 1000;
int sine_step = 0;
int pwm_counter = 0;

const unsigned char sine[50] = {
    52,57,62,66,70,74,77,80,82,84,85,86,86,
    86,85,83,81,78,75,72,69,65,61,56,52,
    48,44,39,35,31,28,25,22,19,17,15,14,14,
    14,15,16,18,20,23,26,30,34,38,43,48
};

const unsigned char sinetable[256] = {
128,131,134,137,140,143,146,149,152,156,159,162,165,168,171,174,
176,179,182,185,188,191,193,196,199,201,204,206,209,211,213,216,
218,220,222,224,226,228,230,232,234,236,237,239,240,242,243,245,
246,247,248,249,250,251,252,252,253,254,254,255,255,255,255,255,
255,255,255,255,255,255,254,254,253,252,252,251,250,249,248,247,
246,245,243,242,240,239,237,236,234,232,230,228,226,224,222,220,
218,216,213,211,209,206,204,201,199,196,193,191,188,185,182,179,
176,174,171,168,165,162,159,156,152,149,146,143,140,137,134,131,
128,124,121,118,115,112,109,106,103,99, 96, 93, 90, 87, 84, 81,
79, 76, 73, 70, 67, 64, 62, 59, 56, 54, 51, 49, 46, 44, 42, 39,
37, 35, 33, 31, 29, 27, 25, 23, 21, 19, 18, 16, 15, 13, 12, 10,
9, 8, 7, 6, 5, 4, 3, 3, 2, 1, 1, 0, 0, 0, 0, 0,
0, 0, 0, 0, 0, 0, 1, 1, 2, 3, 3, 4, 5, 6, 7, 8,
9, 10, 12, 13, 15, 16, 18, 19, 21, 23, 25, 27, 29, 31, 33, 35,
37, 39, 42, 44, 46, 49, 51, 54, 56, 59, 62, 64, 67, 70, 73, 76,
79, 81, 84, 87, 90, 93, 96, 99, 103,106,109,112,115,118,121,124
};

uint8_t getPitch(uint8_t cur_sample) {
    return ( cur_sample + 10 ) / 50;
}


void pwm_irh() {
    pwm_clear_irq(pwm_gpio_to_slice_num(AUDIO_PIN));
    pwm_counter++;
    if ( pwm_counter > 500 ) {
        pwm_counter = 0;
        sine_step++;
    }
    if ( sine_step > 50 ) {
        sine_step = 0;
    }
    pwm_set_gpio_level(AUDIO_PIN, sinetable[sine_step]);
}

int main(void) {
    stdio_init_all();
    set_sys_clock_khz(176000, true); 
    gpio_set_function(AUDIO_PIN, GPIO_FUNC_PWM);
    int audio_pin_slice = pwm_gpio_to_slice_num(AUDIO_PIN);

    // Setup PWM interrupt to fire when PWM cycle is complete
    pwm_clear_irq(audio_pin_slice);
    pwm_set_irq_enabled(audio_pin_slice, true);
    irq_set_exclusive_handler(PWM_IRQ_WRAP, pwm_irh);
    irq_set_enabled(PWM_IRQ_WRAP, true);

    // Setup PWM for audio output
    pwm_config config = pwm_get_default_config();
    pwm_config_set_clkdiv(&config, 4.0f);
    pwm_config_set_wrap(&config, 250);
    pwm_init(audio_pin_slice, &config, true);

    pwm_set_gpio_level(AUDIO_PIN, 0);

    while(1) {
        __wfi();
    }
}

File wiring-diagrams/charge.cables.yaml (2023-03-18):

cables:

  # LIM => RGB LED
  X01:
    gauge: 1 mm2
    wirecount: 4
    colors: [ RD, GN, BU, BK ]

  # Charge port PE => GND
  X02:
    gauge: 2.5 mm2
    wirecount: 1
    colors: [ GN ]

  # GND from 12V batt => CCS_HVJB
  X03:
    gauge: 2.5 mm2
    wirecount: 1
    colors: [ BK ]

  # CCS_HVJB <-> LIM_4B
  X04:
    gauge: 1 mm2
    wirecount: 5
    colors: [ YE, GN, BU, VT, PK ]

  # LIM Voltage sense board to HVJB (probably inside the CCS HVJB anyway)
  X05:
    gauge: 1 mm2
    wirecount: 2
    colors: [ RD, BK ]

  # 12V power supply to Tesla charger
  X06:
    gauge: 1 mm2
    wirecount: 2
    colors: [ RD, BK ]

  # LIM => 12v-rear, power supply
  X08:
    gauge: 1 mm2
    wirecount: 2
    colors: [ RD, BK ]

  # CCS charge port, 3x live => MCBs
  X09:
    gauge: 2.5 mm2
    wirecount: 3
    colors: [ OG, OG, OG ]

  # CCS charge port, 3x neutral => Tesla
  X10:
    gauge: 2.5 mm2
    wirecount: 3
    colors: [ BU, BU, BU ]

  # MCBs => tesla
  X11:
    gauge: 2.5 mm2
    wirecount: 3
    colors: [ OG, OG, OG ]

  # Tesla DC => DC fuses
  X12:
    gauge: 2.5 mm2
    wirecount: 3
    colors: [ OG, OG, OG ]

  # DC fuses, pos => HVJB
  X13:
    gauge: 2.5 mm2
    wirecount: 3
    colors: [ OG, OG, OG ]

  # Tesla DC neg => HVJB
  X14:
    gauge: 2.5 mm2
    wirecount: 3
    colors: [ OG, OG, OG ]

  # Charge port => lim
  X15:
    gauge: 1 mm2
    wirecount: 2
    colors: [ VT, PK ]

  # CCS charge port HV => CCS HVJB
  X16:
    gauge: 35 mm2
    wirecount: 2
    colors: [ OG, OG ]

  # Chademo charge port HV => HVJB
  X18:
    gauge: 35 mm2
    wirecount: 2
    colors: [ OG, OG ]

  # 12v-rear => lim sense board, 12v supply
  X19:
    gauge: 1 mm2
    wirecount: 2
    colors: [ RD, BK ]

  # 12v-rear J10 <= 12V batt
  X20:
    # FIXME is this gauge right?
    gauge: 6 mm2
    wirecount: 2
    colors: [ RD, BK ]

  # LIM GND
  X22:
    gauge: 1 mm2
    wirecount: 1
    colors: [ BK ]

  # CCS charge controller power
  X23:
    gauge: 1 mm2
    wirecount: 2
    colors: [ RD, BK ]

  # CCS charge controller, LIM CAN
  X24:
    gauge: 1 mm2
    wirecount: 2
    colors: [ PK, VT ]

  X26:
    gauge: 1 mm2
    wirecount: 2
    colors: [ PK, VT ]

  # Tesla case GND
  X27:
    gauge: 1 mm2
    wirecount: 1
    colors: [ GN ]

  # Battery side of CCS contactor => battery side of Chademo contactor
  # This is a busbar inside the rear hvjb
  X28:
    gauge: 35 mm2
    wirecount: 2
    colors: [ OG, OG ]

  # charge contactors in front hvjb => read hvjb
  X29:
    gauge: 35 mm2
    wirecount: 2
    colors: [ OG, OG ]


  X30:
    gauge: 1 mm2
    wirecount: 4
    colors: [ PK, YE, GN, BU ]

  X34:
    gauge: 1 mm2
    wirecount: 1
    colors: [ BK ]

  X35:
    gauge: 70 mm2
    wirecount: 2
    colors: [ OG, OG ]


  

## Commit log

2021-11-30 Add front schematic/pcb
    [12v-front-pcb.kicad_pcb, 12v-front-pcb.sch]
2021-11-30 Add rear pcb
    [12v-rear.kicad_pcb, 12v-rear.sch]
2021-12-04 Add dash vcu
    [12v-rear.kicad_pcb, 12v-rear.sch, dashboard-vcu.kicad_pcb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]
2021-12-05 dash tweaks
    [dashboard-vcu.kicad_pcb, dashboard-vcu.sch]
2021-12-05 Initial testing of driving fuel gauge with pwm and a TIP101
2022-01-07 Split out lighting fuses/relays to separate board
    [12v-lighting.kicad_pcb, 12v-lighting.kicad_sch, 12v-lighting.sch]
2022-01-08 Re-work front PCB
    [12v-front-pcb.kicad_pcb, 12v-front-pcb.kicad_sch, 12v-front-pcb.sch]
2022-01-08 Switch to using Pi Pico for dash vcu
    [dashboard-vcu.kicad_pcb, dashboard-vcu.kicad_sch, dashboard-vcu.sch]
2022-05-12 Start working on functional spec for bms, charge controller, and dashboaord
2022-05-18 Add 12v inventory
2022-05-18 Notes for pico programming
2022-05-18 Add beginnging of BMS code
2022-05-18 12v cabin board
    [12v-front-pcb.kicad_pcb, 12v-front-pcb.kicad_sch, 12v-front-pcb.sch]
2022-05-18 12v lighting
    [12v-lighting.kicad_pcb, 12v-lighting.kicad_sch]
2022-05-18 12v front board
    [12v-front-pcb.kicad_pcb]
2022-05-18 12v rear
    [12v-rear.kicad_pcb, 12v-rear.kicad_sch]
2022-05-18 Functional spec for BMS
2022-05-18 Add functional spec for charge controller
2022-05-18 wiring diagrams
    [mustang.bom.tsv]
2022-05-23 starting to put some shape on the bms code
2022-05-28 Add beginning of BMS circuit.
    [bms.kicad_pcb, bms.kicad_sch]
2022-05-31 v1.0 of BMS finalised. Sent of for fabrication
    [bms-B_Cu.gbl, bms-B_Mask.gbs, bms-B_Paste.gbp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]
2022-06-03 Finalised 12v front PCB design (engine board) and sent for fabrication
    [12v-front-pcb-B_Cu.gbl, 12v-front-pcb-B_Mask.gbs, 12v-front-pcb-B_Paste.gbp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]
2022-06-03 Add 12v-front to wiring diagrams
    [mustang.bom.tsv]
2022-06-04 slight tweaks to bms functional spec
2022-06-07 roughing out various bits of the bms
2022-06-12 Work on reading voltage and temperature readings
2022-06-13 BMS PCB fixes. Serial header for debugging. Heavier traces in certain places. Fix some pico pin connections.
    [bms.kicad_pcb, bms.kicad_sch]
2022-06-13 just some 12v-front backups from having it open
2022-06-14 Cleanup cabin pcb
    [12v-cabin.kicad_pcb, 12v-cabin.kicad_sch, 12v-cabin.sch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]
2022-06-29 Redo gerbers
    [bms-B_Cu.gbl, bms-B_Mask.gbs, bms-B_Paste.gbp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]
2022-06-29 v2 of bms sent off for fabrication
    [bms.csv, bms.kicad_pcb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]
2022-07-11 Fix up initialisation of variables and try getting pack polling to work
    [settings.h]
2022-07-11 Found two more errors in bms. Create version 3
    [bms.kicad_pcb, bms.kicad_sch]
2022-07-29 Fix setup of CAN ports
    [settings.h]
2022-07-30 Various restructuring. Now sending and receiving CAN messages. Added LED flashing.
2022-07-30 Rework front PCB to make more room for relays
    [12v-front-pcb.kicad_pcb, 12v-front-pcb.kicad_sch]
2022-12-05 Split wiring diagrams into individual files to make things more readable
    [mustang.bom.tsv]
2022-12-05 split up CCS_HVJB contactors to individual devices
2022-12-05 Split out charge contactors
2023-01-02 BMS pcb v4
    [bms-B_Cu.gbl, bms-B_Mask.gbs, bms-B_Paste.gbp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]
2023-01-07 12v front backups
2023-01-07 12v lighting backups
    [12v-lighting.kicad_pcb, 12v-lighting.kicad_sch]
2023-01-07 12v rear backups
    [12v-rear.kicad_sch]
2023-01-07 bms backups
2023-01-07 BMS successfully fetching voltage and temperature data
2023-01-07 add some sample messages from simp
2023-01-07 Add lighting wiring diagrams
2023-01-07 Updates to the 12v front pcb
    [12v-front-pcb.kicad_pcb, 12v-front-pcb.kicad_sch]
2023-01-07 gerbers for v4 pcb
2023-01-12 Work on BMS state machine
2023-01-15 various bits of fixing and cleanup
    [settings.h]
2023-01-15 Get status light working as intended. Different flash patterns for standby, drive, charge, and fault
2023-01-17 working on pcb for tail lights
    [tail-lights.kicad_pcb, tail-lights.kicad_sch]
2023-01-19 Get cell delta working. Fix module id off-by-one.
    [settings.h]
2023-01-21 Add inputs for CHARGE_ENABLE and IGNITION_ON. Deal with charge termination. Add logging to state transitions. Change status light mode properly.
2023-01-22 store cellDelta in mV. Simplify status print.
2023-01-22 Adjust status print
2023-01-22 12v-front backups
    [12v-front-pcb.kicad_sch]
2023-01-22 bms pcb backups
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2023-01-22 Dashboard vcu update
    [dashboard-vcu.kicad_pcb, dashboard-vcu.kicad_sch]
2023-03-11 brake pedal, cruise button, new BMS pinout
2023-03-14 BMS updates to functional spec
2023-03-16 Finalise tail-lights. Send off for fab
    [tail-lights-B_Cu.gbl, tail-lights-B_Mask.gbs, tail-lights-B_Paste.gbp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]
2023-03-16 Errors in charge/drive mode
    [12v-front-pcb.kicad_pcb, 12v-front-pcb.kicad_sch]
2023-03-18 lighting board. Add reverse light. Fix up a couple of issues.
    [12v-lighting.kicad_pcb, 12v-lighting.kicad_sch]
2023-03-18 Fixing issues on 12-front. lots of updates to wiring diagrams
    [12v-front-pcb.kicad_sch]
2023-03-18 minor tweaks
    [12v-rear.kicad_sch]
2023-03-20 start outlining charge controller code
2023-03-23 Set up build environment. Add other CAN bus interfaces. Listen for IN1/IN2 signals (chademo). Handle inbound ChaDeMo CAN frames.
2023-03-23 Add watchdog to bms
2023-04-09 random updates
    [bms.kicad_pcb, bms.kicad_sch]
2023-04-09 kicad backups
    [12v-rear.kicad_pcb]
2023-04-09 Make charger build before going further
2023-04-15 Add current ramping to chademo and read messages from BMS
2023-04-16 Calculate SoC. Reset ISA shunt after charging to 100%
    [settings.h]
2023-04-17 Work a bit on charge_inhibit for chademo
2023-04-28 fix vehicle status reporting
    [chademo.cpp]
2023-04-30 Deal with CC/CV charging phases. refactor some error handling
    [chademo.cpp]
2023-04-30 Transmit measured voltage as part of BMS messages
2023-05-01 Deal with CC/CV windows. Deal with charge termination
2023-05-01 More debug msgs + some minor fixes
    [chademo.cpp]
2023-12-05 Start writing test cases for BMS
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2023-12-09 rework on 12v front pcb
    [12v-front-pcb-B_Cu.gbl, 12v-front-pcb-B_Mask.gbs, 12v-front-pcb-B_Paste.gbp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]
2023-12-09 Work BMS test cases
2024-01-25 Send tail lights v2 for fabrication
    [tail-lights-B_Cu.gbl, tail-lights-B_Mask.gbs, tail-lights-B_Paste.gbp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]
2024-02-29 Move bms code over to separate repo
    [bms-B_Cu.gbl, bms-B_Mask.gbs, bms-B_Paste.gbp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]

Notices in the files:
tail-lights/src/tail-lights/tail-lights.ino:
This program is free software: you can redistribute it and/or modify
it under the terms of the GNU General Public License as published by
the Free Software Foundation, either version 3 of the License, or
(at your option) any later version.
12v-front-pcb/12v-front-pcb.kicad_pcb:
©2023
